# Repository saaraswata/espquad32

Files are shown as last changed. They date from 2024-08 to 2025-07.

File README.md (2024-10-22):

# ESP32-Quadcopter

### Introduction

**ESP32-Quadcopter** is an open source solution based on Espressif ESP32/ESP32-S2/ESP32-S3 Wi-Fi chip, which can be controlled by a mobile APP or gamepad over **Wi-Fi** connection. ESP32-QUADCOPTER comes with **simple hardware**, **clear and extensible code architecture**, and therefore this project can be used in **STEM education** and other fields. The main code is ported from **Crazyflie** open source project with **GPL3.0** protocol.

> Currently support ESP32, ESP32S2, ESP32S3, please using ESP-IDF [release/v4.4](https://docs.espressif.com/projects/esp-idf/en/release-v4.4/esp32/get-started/index.html) branch as your develop environment

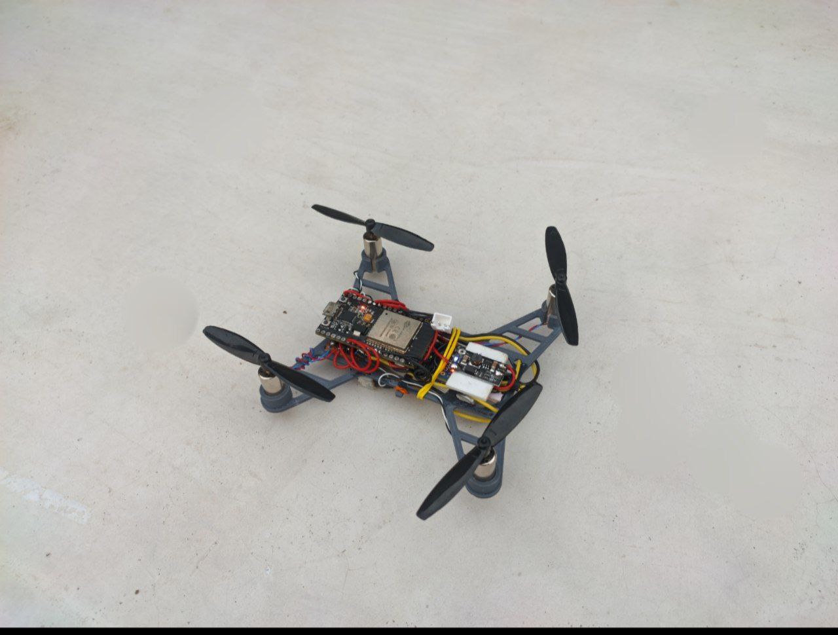
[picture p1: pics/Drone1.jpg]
ESP32-QUADCOPTER


For more information, please check the sections below:
* **Getting Started**: 
* **Hardware Schematic**：
* **iOS APP Source code**: [ESP-Drone-iOS](https://github.com/EspressifApps/ESP-Drone-iOS)
* **Android APP Source code**: [ESP-Drone-Android](https://github.com/EspressifApps/ESP-Drone-Android)

### Features

1. Stabilize Mode
2. Height-hold Mode
3. Altitude-hold Mode
4. Position-hold Mode
5. APP Control
6. CFclient Supported
7. ESP-BOX3 Joystick Control (through esp-now)

Note: to implement Altitude-hold/Height-hold/Position-hold mode, extension boards are needed. For more information, see Hardware Reference. 

### Third Party Copyrighted Code

Additional third party copyrighted code is included under the following licenses.

| Component | License | Origin |Commit ID |
| :---:  | :---: | :---: |:---: |
| core/crazyflie | GPL3.0  |[Crazyflie](https://github.com/bitcraze/crazyflie-firmware) |tag_2021_01 b448553|
| lib/dsp_lib |  | [esp32-lin](https://github.com/whyengineer/esp32-lin/tree/master/components/dsp_lib) |6fa39f4c|

### Support Policy

Any kind of modifications as long as plausible are welcome. Support till 2028.

### THANKS

1. Thanks to Bitcraze for the great [Crazyflie project](https://www.bitcraze.io/%20).
2. Thanks to Espressif for the powerful [ESP-IDF framework](https://docs.espressif.com/projects/esp-idf/en/latest/esp32s2/get-started/index.html).
3. Thanks to WhyEngineer for the useful [ESP-DSP lib](https://github.com/whyengineer/esp32-lin/tree/master/components/dsp_lib).
4. Thanks to Espressif for the ESP-Drone port of Crazyflie firmware.

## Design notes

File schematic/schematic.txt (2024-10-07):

ESP32 GPIO | MPU6050
3v3        |  Vin
Gnd        |  Gnd
32         |  SDA
33         |  SCL
23         |  INT

ESP32 GPIO |   ESC
16         |  Mot_1  
4          |  Mot_2
12         |  Mot_3
14         |  Mot_4

MPU6050 | MS5611
3v3     |  3v3
Gnd     |  Gnd
SDA     |  SDA
SCL     |  SCL

Info about Motors:
Using 8520 brushless Motors. If using 716/715 coreless motors then select 715 from Menuconfig
Mot_1 and Mot_3: CCW
Mot_2 and Mot_4: CW

Info about MPU6050 Placement and Direction:
MPU6050 can be placed anywhere on the drone. The Pinout of the MPU6050 should be on the right side, and this is the position where forward of you is forward of the drone.

NOTE:
* Connecting INT pin is only required for ESP32. ESP32 S2 and S3 don't need this pin to be connected.
* Use High Current rate batteries. I'm using Orange 3.8v 90C/180C 550mah (Best choice) AND/OR Bonka 3.7v 600mah 25C Lipo battery (not so preferred, but flies)
* Pins can be changed from menuconfig

I am getting approx 5 mins of flight time with both the batteries but the drone flies much higher and better with Orange 3.8v 90C/180C lipo cell.
You can also use 1000mah 30C 3.7v batteries.

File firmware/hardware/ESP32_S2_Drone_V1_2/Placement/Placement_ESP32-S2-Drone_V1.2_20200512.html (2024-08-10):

D:\WORK\#31436_ESP32-S2-ESPlane-KIT_M_V1.0_N_XX_20200325_V0.1\#31436_ESP32-S2-ESPlane-KIT_M_V1.2_N_XX_20200511_V0.3\02_PCB/PCB_ESP32-S2-Drone_V1.2_20200512.pcb Create in 2020/5/12 17:13:59 Total components = 203 component(s)

Component Report
NO. | RefDes | PartDecal | Pins | Layer | Orient | PositionX | PositionY | IsSMD
1 | C1 | C0603 | 2 | Top | 180 | 1571.554 | 2462.404 | Yes
2 | C2 | C0402 | 2 | Top | 90 | 1685.304 | 2562.104 | Yes
3 | C3 | C0603 | 2 | Top | 180 | 1555.454 | 2230.404 | Yes
4 | C4 | C0402 | 2 | Top | 270 | 1923.504 | 2559.904 | Yes
5 | C5 | C0402 | 2 | Top | 270 | 1771.004 | 2562.104 | Yes
6 | C6 | C0603 | 2 | Top | 0 | 2787.933 | 2016.722 | Yes
7 | C7 | C0402 | 2 | Top | 0 | 2808.406 | 1922.234 | Yes
8 | C8 | C0603 | 2 | Top | 180 | 2671.004 | 2016.722 | Yes
9 | C9 | C0402 | 2 | Top | 90 | 2750.925 | 1943.888 | Yes
10 | C10 | C0603 | 2 | Top | 180 | 1711.454 | 2230.404 | Yes
11 | C11 | C0603 | 2 | Top | 180 | 1706.504 | 2462.404 | Yes
12 | C12 | C0603 | 2 | Top | 180 | 1426.004 | 2117.254 | Yes
13 | C13 | C0402 | 2 | Top | 0 | 2231.004 | 2304.754 | Yes
14 | C14 | C0603 | 2 | Top | 90 | 2369.754 | 2361.004 | Yes
15 | C15 | C0603 | 2 | Top | 90 | 2169.754 | 2403.504 | Yes
16 | C16 | C0603 | 2 | Top | 180 | 2409.843 | 1237.402 | Yes
17 | C17 | C0402 | 2 | Top | 180 | 2398.031 | 1188.189 | Yes
18 | C18 | C0402 | 2 | Top | 270 | 1571.260 | 1214.173 | Yes
19 | C19 | C0402 | 2 | Top | 270 | 1852.254 | 2286.004 | Yes
20 | C20 | C0402 | 2 | Top | 0 | 2028.839 | 2377.254 | Yes
21 | C21 | C0402 | 2 | Top | 90 | 1959.604 | 2393.504 | Yes
22 | C22 | C0402 | 2 | Top | 180 | 1918.504 | 2141.004 | Yes
23 | C23 | C0402 | 2 | Top | 0 | 1139.370 | 1915.354 | Yes
24 | C24 | C0402 | 2 | Top | 0 | 1139.754 | 1604.754 | Yes
25 | D1 | SOD523 | 2 | Top | 315 | 1382.254 | 1399.754 | Yes
26 | D2 | SOD523 | 2 | Top | 45 | 1389.754 | 2547.254 | Yes
27 | D3 | SOD323 | 2 | Top | 90 | 2376.004 | 2237.254 | Yes
28 | D4 | SOD523 | 2 | Top | 135 | 2549.754 | 2552.254 | Yes
29 | D5 | SOD523 | 2 | Top | 0 | 2744.754 | 1419.754 | Yes
30 | D6 | LED3010-S | 3 | Top | 0 | 1476.378 | 2814.961 | Yes
31 | D7 | LED3010-S | 3 | Top | 180 | 1476.378 | 1122.047 | Yes
32 | D8 | LED3010-S | 3 | Top | 0 | 2460.630 | 2814.961 | Yes
33 | D9 | LED3010-S | 3 | Top | 180 | 2460.630 | 1122.047 | Yes
34 | FB1 | L0603 | 2 | Top | 90 | 2409.754 | 1328.504 | Yes
35 | H1 | P_2X1 | 1 | Bottom | 135 | 2814.964 | 2657.484 | Yes
36 | H58 | P_2X1 | 1 | Bottom | 45 | 708.661 | 3346.457 | Yes
37 | H59 | P_2X1 | 1 | Bottom | 45 | 1279.528 | 2814.961 | Yes
38 | H60 | P_2X1 | 1 | Bottom | 45 | 2657.480 | 1122.047 | Yes
39 | H61 | P_2X1 | 1 | Bottom | 45 | 3228.346 | 590.551 | Yes
40 | H62 | P_2X1 | 1 | Bottom | 135 | 1122.047 | 1279.528 | Yes
41 | H63 | P_2X1 | 1 | Bottom | 45 | 1122.047 | 2657.480 | Yes
42 | H65 | P_2X1 | 1 | Bottom | 45 | 3346.457 | 708.661 | Yes
43 | H66 | P_2X1 | 1 | Bottom | 135 | 2657.480 | 2814.961 | Yes
44 | H67 | P_2X1 | 1 | Bottom | 135 | 1279.528 | 1122.047 | Yes
45 | H68 | P_2X1 | 1 | Bottom | 135 | 590.551 | 708.661 | Yes
46 | H69 | P_2X1 | 1 | Bottom | 45 | 590.551 | 3228.346 | Yes
47 | H70 | P_2X1 | 1 | Bottom | 45 | 2814.961 | 1279.528 | Yes
48 | H71 | P_2X1 | 1 | Bottom | 135 | 3346.457 | 3228.346 | Yes
49 | H72 | P_2X1 | 1 | Bottom | 135 | 708.661 | 590.551 | Yes
50 | H73 | P_2X1 | 1 | Bottom | 135 | 3228.346 | 3346.457 | Yes
51 | J1 | USB_5P_MICRO_F | 11 | Top | 180 | 2638.504 | 2303.504 | No
52 | J2 | FFC24-0P5 | 26 | Top | 180 | 1968.504 | 2736.220 | Yes
53 | J3 | A2005HWV-S-XP-A | 16 | Top | 270 | 2460.630 | 1751.969 | No
54 | J4 | A2005HWV-S-XP-A | 16 | Top | 270 | 1476.378 | 1751.969 | No
55 | J5 | CON2X1_1P5_SMT_ZH-2A_DIP | 4 | Top | 45 | 2678.504 | 2678.504 | No
56 | J6 | CON2X1_1P5_SMT_ZH-2A_DIP | 4 | Top | 315 | 2678.504 | 1258.504 | No
57 | J7 | CON2X1_2P0_SMT_PH2A-S-A | 4 | Top | 270 | 1478.346 | 2288.504 | Yes
58 | J8 | CON2X1_1P5_SMT_ZH-2A_DIP | 4 | Top | 225 | 1258.504 | 1258.504 | No
59 | J9 | CON2X1_1P5_SMT_ZH-2A_DIP | 4 | Top | 135 | 1258.504 | 2678.504 | No
60 | J10 | A2005HWV-S-XP-A | 16 | Top | 270 | 1476.378 | 463.219 | No
61 | J11 | A2005HWV-S-XP-A | 16 | Top | 270 | 2460.630 | 463.219 | No
62 | Q3 | SOT-23-3 | 3 | Top | 180 | 1291.334 | 2033.504 | Yes
63 | Q4 | SOT-23-3 | 3 | Top | 0 | 1218.504 | 1512.004 | Yes
64 | Q5 | SOT-23-3 | 3 | Top | 270 | 1518.504 | 2667.254 | Yes
65 | Q6 | SOT-23-3 | 3 | Top | 90 | 2418.504 | 2667.504 | Yes
66 | Q7 | SOT-23-3 | 3 | Top | 0 | 2718.504 | 1512.004 | Yes
67 | R1 | R0402 | 2 | Top | 180 | 2533.504 | 2143.504 | Yes
68 | R3 | R0402 | 2 | Top | 0 | 2454.754 | 2143.504 | Yes
69 | R5 | R0402 | 2 | Top | 90 | 1868.404 | 2559.904 | Yes
70 | R6 | R0402 | 2 | Top | 270 | 1736.904 | 2562.104 | Yes
71 | R7 | R0402 | 2 | Top | 90 | 2709.193 | 1943.888 | Yes
72 | R8 | R0402 | 2 | Top | 0 | 2808.012 | 1963.967 | Yes
73 | R9 | R0402 | 2 | Top | 0 | 2646.201 | 1929.321 | Yes
74 | R10 | R0402 | 2 | Top | 0 | 2646.201 | 1964.754 | Yes
75 | R11 | R0402 | 2 | Top | 90 | 1321.260 | 1581.890 | Yes
76 | R12 | R0402 | 2 | Top | 90 | 1356.693 | 1581.890 | Yes
77 | R13 | R0402 | 2 | Top | 180 | 1232.254 | 1604.754 | Yes
78 | R14 | R0402 | 2 | Top | 180 | 1675.504 | 2619.904 | Yes
79 | R15 | R0402 | 2 | Top | 90 | 2583.996 | 1996.348 | Yes
80 | R16 | R0402 | 2 | Top | 270 | 2583.996 | 1916.148 | Yes
81 | R17 | R0402 | 2 | Top | 0 | 1253.504 | 2123.504 | Yes
82 | R18 | R0402 | 2 | Top | 180 | 2231.004 | 2267.854 | Yes
83 | R19 | R0402 | 2 | Top | 0 | 1139.754 | 1871.004 | Yes
84 | R20 | R0402 | 2 | Top | 90 | 2287.254 | 2288.504 | Yes
85 | R21 | R0402 | 2 | Top | 180 | 1538.976 | 1357.480 | Yes
86 | R22 | R0402 | 2 | Top | 90 | 1536.614 | 1214.173 | Yes
87 | R23 | R0402 | 2 | Top | 180 | 2381.004 | 2563.504 | Yes
88 | R24 | R0402 | 2 | Top | 90 | 2622.254 | 1529.754 | Yes
89 | R25 | R0402 | 2 | Top | 180 | 1538.976 | 1397.638 | Yes
90 | R26 | R0402 | 2 | Top | 180 | 1516.004 | 2763.504 | Yes
91 | R27 | R0402 | 2 | Top | 0 | 2018.604 | 2121.004 | Yes
92 | R28 | R0402 | 2 | Top | 0 | 1887.254 | 2377.254 | Yes
93 | R29 | R0402 | 2 | Top | 90 | 1448.504 | 1214.754 | Yes
94 | R30 | R0402 | 2 | Top | 180 | 2499.754 | 2763.504 | Yes
95 | R31 | R0402 | 2 | Top | 0 | 2476.772 | 1188.189 | Yes
96 | R32 | R0402 | 2 | Top | 270 | 2086.004 | 2360.504 | Yes
97 | R33 | R0402 | 2 | Top | 90 | 2086.004 | 2280.504 | Yes
98 | R34 | R0402 | 2 | Top | 0 | 1282.254 | 1759.754 | Yes
99 | R35 | R0402 | 2 | Top | 90 | 1344.754 | 1702.254 | Yes
100 | SW1 | SW4_3X3P5X1P1_SMT | 6 | Top | 270 | 1141.704 | 2047.244 | No
101 | SW2 | SW4_3X3P5X1P1_SMT | 6 | Top | 270 | 1141.732 | 1740.157 | No
102 | T1 | K_3X2 | 1 | Top | 0 | 68.504 | 2242.504 | No
103 | T2 | K_3X2 | 1 | Top | 0 | 68.504 | 2095.504 | No
104 | T3 | K_3X2 | 1 | Top | 0 | 720.472 | 2242.504 | No
105 | T4 | K_3X2 | 1 | Top | 0 | 720.472 | 2095.504 | No
106 | T5 | K_3X2 | 1 | Top | 0 | 68.504 | 1841.504 | No
107 | T6 | K_3X2 | 1 | Top | 0 | 68.504 | 1694.504 | No
108 | T7 | K_3X2 | 1 | Top | 0 | 720.474 | 1841.504 | No
109 | T8 | K_3X2 | 1 | Top | 0 | 720.472 | 1694.504 | No
110 | T9 | K_3X2 | 1 | Top | 180 | 1648.504 | 3512.254 | No
111 | T10 | K_3X2 | 1 | Top | 180 | 1648.504 | 3366.004 | No
112 | T11 | K_3X2 | 1 | Top | 180 | 3868.504 | 2242.504 | No
113 | T12 | K_3X2 | 1 | Top | 180 | 3868.504 | 2094.754 | No
114 | T13 | K_3X2 | 1 | Top | 180 | 2276.504 | 3512.254 | No
115 | T14 | K_3X2 | 1 | Top | 180 | 2276.504 | 3366.004 | No
116 | T15 | K_3X2 | 1 | Top | 180 | 3868.504 | 1841.504 | No
117 | T16 | K_3X2 | 1 | Top | 180 | 3868.504 | 1694.754 | No
118 | T17 | K_3X2 | 1 | Top | 0 | 3216.504 | 2242.504 | No
119 | T18 | K_3X2 | 1 | Top | 0 | 3216.504 | 2095.504 | No
120 | T19 | K_3X2 | 1 | Top | 0 | 3216.504 | 1841.504 | No
121 | T20 | K_3X2 | 1 | Top | 0 | 3216.504 | 1694.504 | No
122 | T21 | SMD_3X6 | 1 | Top | 225 | 3359.055 | 495.669 | No
123 | T22 | HOLE_0P6 | 1 | Top | 0 | 717.649 | 2527.559 | No
124 | T23 | SMD_3X6 | 1 | Top | 45 | 3881.102 | 136.220 | No
125 | T24 | SMD_3X6 | 1 | Top | 135 | 3813.386 | 3888.583 | No
126 | T25 | SMD_3X6 | 1 | Top | 315 | 3446.063 | 3375.591 | No
127 | T26 | SMD_3X6 | 1 | Top | 225 | 47.638 | 3812.205 | No
128 | T27 | SMD_3X6 | 1 | Top | 45 | 585.039 | 3433.071 | No
129 | T28 | SMD_3X6 | 1 | Top | 135 | 497.638 | 582.677 | No
130 | T29 | SMD_3X6 | 1 | Top | 315 | 124.409 | 45.669 | No
131 | T30 | HOLE_0P6 | 1 | Top | 0 | 717.649 | 2500.000 | No
132 | T31 | HOLE_0P6 | 1 | Top | 0 | 717.649 | 2472.441 | No
133 | T32 | HOLE_0P6 | 1 | Top | 0 | 717.649 | 2417.323 | No
134 | T33 | HOLE_0P6 | 1 | Top | 0 | 717.649 | 1519.685 | No
135 | T34 | HOLE_0P6 | 1 | Top | 0 | 717.649 | 1492.126 | No
136 | T35 | HOLE_0P6 | 1 | Top | 0 | 717.649 | 1464.567 | No
137 | T36 | HOLE_0P6 | 1 | Top | 0 | 717.649 | 1409.449 | No
138 | T37 | HOLE_0P6 | 1 | Top | 0 | 717.649 | 1437.008 | No
139 | T38 | HOLE_0P6 | 1 | Top | 0 | 1076.772 | 1519.685 | No
140 | T39 | HOLE_0P6 | 1 | Top | 0 | 1076.772 | 1492.126 | No
141 | T40 | HOLE_0P6 | 1 | Top | 0 | 1076.772 | 1464.567 | No
142 | T41 | HOLE_0P6 | 1 | Top | 0 | 1076.772 | 1409.449 | No
143 | T42 | HOLE_0P6 | 1 | Top | 0 | 1076.772 | 1437.008 | No
144 | T43 | HOLE_0P6 | 1 | Top | 0 | 1076.772 | 2531.496 | No
145 | T44 | HOLE_0P6 | 1 | Top | 0 | 1076.772 | 2503.937 | No
146 | T45 | HOLE_0P6 | 1 | Top | 0 | 1076.772 | 2476.378 | No
147 | T46 | HOLE_0P6 | 1 | Top | 0 | 1076.772 | 2448.819 | No
148 | T47 | HOLE_0P6 | 1 | Top | 0 | 1076.772 | 2421.260 | No
149 | T48 | HOLE_0P6 | 1 | Top | 0 | 3219.359 | 2531.496 | No
150 | T49 | HOLE_0P6 | 1 | Top | 0 | 3219.359 | 2503.937 | No
151 | T50 | HOLE_0P6 | 1 | Top | 0 | 3219.359 | 2476.378 | No
152 | T51 | HOLE_0P6 | 1 | Top | 0 | 3219.359 | 2448.819 | No
153 | T52 | HOLE_0P6 | 1 | Top | 0 | 3219.359 | 2421.260 | No
154 | T53 | HOLE_0P6 | 1 | Top | 0 | 3219.359 | 1515.748 | No
155 | T54 | HOLE_0P6 | 1 | Top | 0 | 3219.359 | 1488.189 | No
156 | T55 | HOLE_0P6 | 1 | Top | 0 | 3219.359 | 1460.630 | No
157 | T56 | HOLE_0P6 | 1 | Top | 0 | 3219.359 | 1433.071 | No
158 | T57 | HOLE_0P6 | 1 | Top | 0 | 3219.359 | 1405.512 | No
159 | T58 | HOLE_0P6 | 1 | Top | 0 | 717.649 | 2444.882 | No
160 | T59 | HOLE_0P6 | 1 | Top | 0 | 2860.236 | 1519.685 | No
161 | T60 | HOLE_0P6 | 1 | Top | 0 | 2860.236 | 1492.126 | No
162 | T61 | HOLE_0P6 | 1 | Top | 0 | 2860.236 | 1464.567 | No
163 | T62 | HOLE_0P6 | 1 | Top | 0 | 2860.236 | 1437.008 | No
164 | T63 | HOLE_0P6 | 1 | Top | 0 | 2860.236 | 1409.449 | No
165 | T64 | HOLE_0P6 | 1 | Top | 0 | 2860.236 | 2531.496 | No
166 | T65 | HOLE_0P6 | 1 | Top | 0 | 2860.236 | 2503.937 | No
167 | T66 | HOLE_0P6 | 1 | Top | 0 | 2860.236 | 2476.378 | No
168 | T67 | HOLE_0P6 | 1 | Top | 0 | 2860.236 | 2448.819 | No
169 | T68 | HOLE_0P6 | 1 | Top | 0 | 2860.236 | 2421.260 | No
170 | T69 | HOLE_0P6 | 1 | Top | 0 | 1549.291 | 1074.803 | No
171 | T70 | HOLE_0P6 | 1 | Top | 0 | 1576.850 | 1074.803 | No
172 | T71 | HOLE_0P6 | 1 | Top | 0 | 1604.409 | 1074.803 | No
173 | T72 | HOLE_0P6 | 1 | Top | 0 | 1631.969 | 1074.803 | No
174 | T73 | HOLE_0P6 | 1 | Top | 0 | 1549.291 | 925.197 | No
175 | T74 | HOLE_0P6 | 1 | Top | 0 | 1576.850 | 925.197 | No
176 | T75 | HOLE_0P6 | 1 | Top | 0 | 1604.409 | 925.197 | No
177 | T76 | HOLE_0P6 | 1 | Top | 0 | 1631.969 | 925.197 | No
178 | T77 | HOLE_0P6 | 1 | Top | 0 | 2305.315 | 925.197 | No
179 | T78 | HOLE_0P6 | 1 | Top | 0 | 2332.874 | 925.197 | No
180 | T79 | HOLE_0P6 | 1 | Top | 0 | 2360.433 | 925.197 | No
181 | T80 | HOLE_0P6 | 1 | Top | 0 | 2387.992 | 925.197 | No
182 | T81 | HOLE_0P6 | 1 | Top | 0 | 2305.315 | 1074.803 | No
183 | T82 | HOLE_0P6 | 1 | Top | 0 | 2332.874 | 1074.803 | No
184 | T83 | HOLE_0P6 | 1 | Top | 0 | 2360.433 | 1074.803 | No
185 | T84 | HOLE_0P6 | 1 | Top | 0 | 2387.992 | 1074.803 | No
186 | T85 | HOLE_0P6 | 1 | Top | 0 | 1913.386 | 3464.567 | No
187 | T86 | HOLE_0P6 | 1 | Top | 0 | 1940.945 | 3464.567 | No
188 | T87 | HOLE_0P6 | 1 | Top | 0 | 1968.504 | 3464.567 | No
189 | T88 | HOLE_0P6 | 1 | Top | 0 | 1996.063 | 3464.567 | No
190 | T89 | HOLE_0P6 | 1 | Top | 0 | 2023.622 | 3464.567 | No
191 | T91 | HOLE_0P6 | 1 | Top | 0 | 1913.386 | 2862.205 | No
192 | T92 | HOLE_0P6 | 1 | Top | 0 | 1940.945 | 2862.205 | No
193 | T93 | HOLE_0P6 | 1 | Top | 0 | 1968.504 | 2862.205 | No
194 | T94 | HOLE_0P6 | 1 | Top | 0 | 1996.063 | 2862.205 | No
195 | T95 | HOLE_0P6 | 1 | Top | 0 | 2023.622 | 2862.205 | No
196 | U1 | SOT23-6 | 6 | Top | 270 | 2493.504 | 2253.504 | Yes
197 | U2 | SOT-23-5 | 5 | Top | 90 | 1500.354 | 2313.104 | Yes
198 | U3 | QFN28_0P5_5 | 29 | Top | 180 | 2688.720 | 1776.959 | Yes
199 | U4 | SOT-23-5 | 5 | Top | 90 | 1656.354 | 2313.104 | Yes
200 | U5 | DFN3030-8 | 9 | Top | 270 | 2264.754 | 2392.254 | Yes
201 | U6 | ESP32-S2-WROVER | 43 | Top | 180 | 2322.835 | 834.646 | Yes
202 | U7 | QFN24_0P5_4_A | 24 | Top | 180 | 1968.504 | 2256.204 | Yes
203 | U8 | SOT363 | 6 | Top | 90 | 1284.754 | 1689.754 | Yes

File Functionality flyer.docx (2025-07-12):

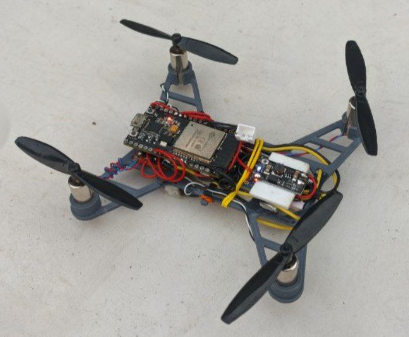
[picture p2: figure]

#### ESP32-Quadcopter Drone

ESP32-Quadcopter is a palm-sized drone project built using ESP32 Wi-Fi microcontrollers, custom-made flight controller and ESC (Electronic Speed Controller) PCBs, and is developed using ESP-IDF. The drone is designed for control via a mobile app over Wi-Fi, and is cost-efficiency, with simple hardware and clear, extensible code architecture.

Why Drones?

Drones are at the forefront of future technology. From agriculture to logistics, defence to filmmaking, autonomous and semi-autonomous drones are reshaping how tasks are approached across numerous industries. As the number of fields adopting drone technology continues to grow, early exposure to these systems becomes essential for staying prepared and contributing meaningfully to the next wave of innovation.

##### Features and Hardware:

Modes | Description | Modules
Stabilize Mode | Maintains stable flight using accelerometer and gyroscopic sensor data. | MPU6050 IMU (Inertial Measurement Unit)
Height-hold Mode | Maintains a fixed flight height using Time-of-flight (ToF) distance sensor data. | VL53L0X/VL53L1X ToF ranging sensor
Altitude-hold Mode | Maintains constant altitude relative to sea level using barometric data. | BMP280 or MS5611 Barometric pressure sensor
Position-hold Mode | Holds drone at a set position using optical flow sensor and Time-of-flight (ToF) distance sensor data. | PMW3901MB-TXQT optical motion tracking sensor, VL53L0X/VL53L1X ToF ranging sensor
Hover Mode | Holds drone at set position and height using optical flow sensor and Time-of-flight (ToF) distance sensor data. | PMW3901MB-TXQT optical motion tracking sensor, VL53L0X/VL53L1X ToF ranging sensor
App Control | Operate and fine-tune the drone via a mobile app. Connect to the drone using a phone via Wi-Fi. | Wi-Fi enabled ESP32 microcontroller
CFclient Supported | Uses Crazyflie’s flight control and tuning software. | Crazyflie client software

##### Potential use-cases:

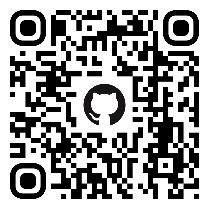
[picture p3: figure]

1. STEM Education: Learn about embedded systems, flight control, sensor integration, and wireless communication in a cost-efficient way while making this project.

YouTube GitHub

2. Recreational Flying and Drone Racing: Enjoy remote-controlled flight using a phone or joystick.

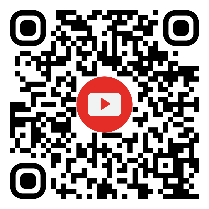
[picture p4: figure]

3. Disaster Rescue: Its small form-factor allows entry into collapsed buildings for gathering information.

4. Emergency Deliveries: Can be quickly deployed to deliver medicines and vaccines over short distances in times of emergency.

5. Agricultural Surveying: Can be adapted for crop health analysis or livestock monitoring over small farmland areas using thermal or NDVI cameras.

6. Environmental Monitoring: Attach temperature, gas, or air quality sensors to monitor environmental conditions in hard-to reach areas like forests, rooftops, or industrial sites.

7. Aerial Photography/Videography and Surveillance: With a lightweight camera module, this drone can capture images or videos from unique angles for documentation, mapping, or remote surveillance.

8. Plug-and-play kits: Can be made into an intuitive plug-and-play assembly kit for children to help them make their own drones by simply connecting the various modules and parts.

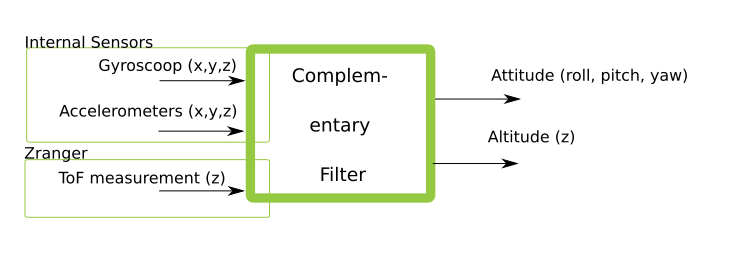
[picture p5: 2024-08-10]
firmware/docs/_static/Schematic-overview-of-inputs-and-outputs-of-the-Complementary-filter.png

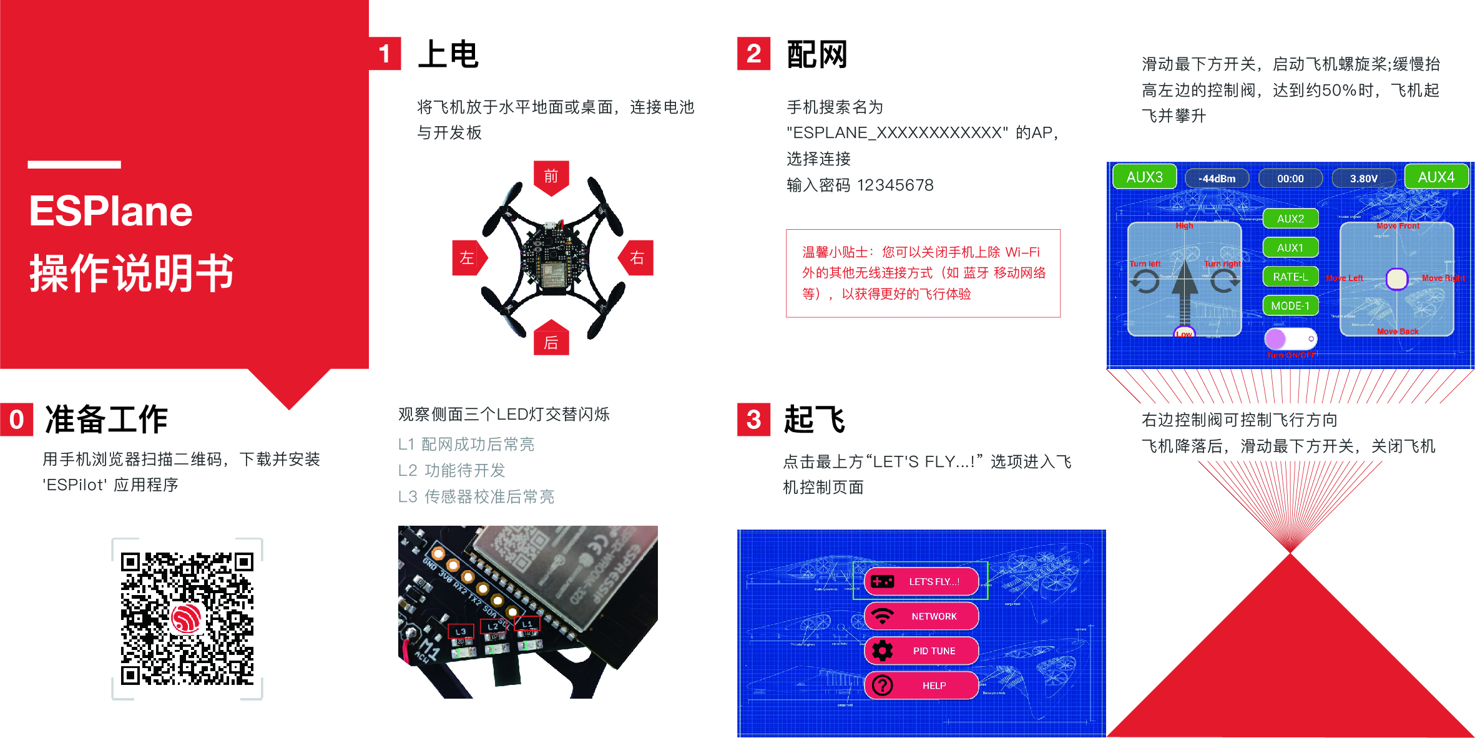
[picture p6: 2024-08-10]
firmware/docs/_static/esplane_v1_specification.jpg

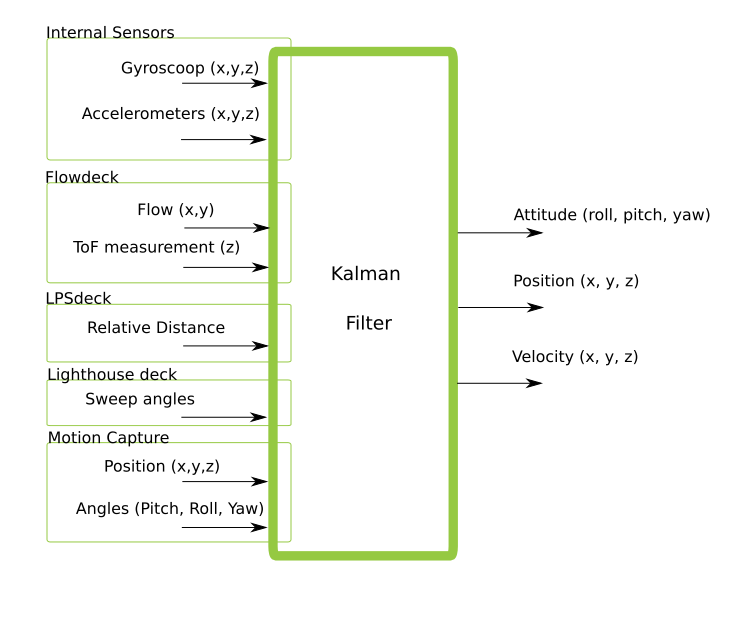
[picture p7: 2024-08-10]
firmware/docs/_static/Schematic-overview-of-inputs-and-outputs-of-the-Extended-Kalman-Filter.png

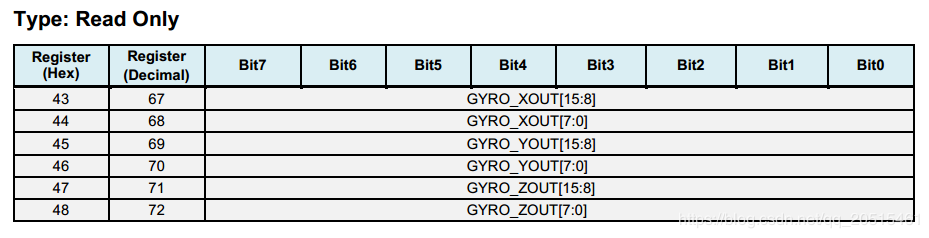
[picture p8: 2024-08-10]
firmware/docs/_static/REG_43_48.png

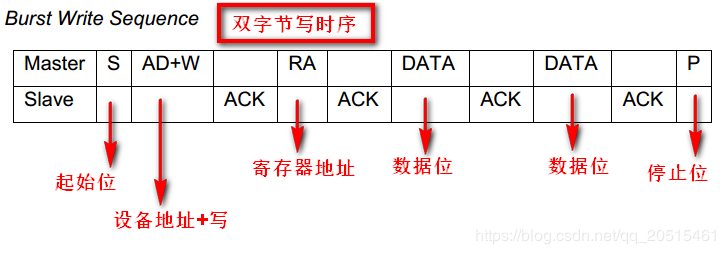
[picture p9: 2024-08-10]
firmware/docs/_static/burst_write_sequence.png

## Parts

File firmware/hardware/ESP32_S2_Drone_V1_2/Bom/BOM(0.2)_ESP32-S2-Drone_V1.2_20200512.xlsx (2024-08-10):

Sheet: ESP32-S2-Drone
BOM(V0.2)_ESP32-S2-Drone_V1.2
ID | Qty | Ref Des | Value | Package | Description | Manufacturer | Manufacturer Part # | Notes
1 | 8 | C1,C3,C10,C11,C12,C14,C15,C16 | 10uF/10V | C0603 | 陶瓷电容
2 | 9 | C2,C4,C5,C7,C9,C17,C18,C19,C21 | 0.1uF/10V | C0402 | 陶瓷电容
3 | 2 | C6,C8 | 4.7uF/10V | C0603 | 陶瓷电容
4 | 1 | C13 | 470pF/25V | C0402 | 陶瓷电容
5 | 1 | C20 | 10nF/25V | C0402 | 陶瓷电容
6 | 1 | C22 | 2.2nF/25V | C0402 | 陶瓷电容
7 | 0 | C23,C24 | 0.1uF/10V(NC) | C0402 | 陶瓷电容 |  |  | 不贴件
8 | 4 | D1,D2,D4,D5 | 1N4148WT | SOD523 | 开关二极管 | 长电科技 | 1N4148WT
9 | 1 | D3 | BAT60B | SOD323 | 肖特基二极管 | Infineon | BAT60B
10 | 1 | D6 | LED-WHT | LED3010-S | LED,白色 | Everlight | 12-21/T3D-APQHY/2C
11 | 1 | D7 | LED-BLE | LED3010-S | LED,蓝色 | Everlight | 12-21/BHC-ZL2N1TY/2C
12 | 1 | D8 | LED-RED | LED3010-S | LED,红色 | Everlight | 12-21/R8C-AN1P2B/2D
13 | 1 | D9 | LED-GRN | LED3010-S | LED,绿色 | Everlight | 12-21/GHC-YQ1R1B18Y/2C
14 | 1 | FB1 | BLM18SG331TN1D | L0603 | 磁珠,330R at 100MHz,1A | Murata | BLM18SG331TN1D
15 | 1 | J1 | USB-MICRO-B | USB_5P_MICRO_F | USB MicroB 连接器,四脚插板,无柱,卷边
16 | 1 | J2 | FFC-24P | FFC24-0P5 | FPC连接器,24P,间距0.5MM,翻盖式,下接
17 | 4 | J3,J4,J10,J11 | CON8-S-2P54 | A2005HWV-S-XP-A | 单排排母,8P,间距2.0mm,错位贴片,A型 | 长江连接器 | A2005HWV-S-8P-A
18 | 0 | J5,J6,J8,J9 | CON2-SB-ZH(NC) | CON2X1_1P5_SMT_ZH-2A_DIP | 针座,2P,ZH,侧入贴片 |  |  | 不贴件
19 | 1 | J7 | CON2-SB-PH | CON2X1_2P0_SMT_PH2A-S-A | 针座,2P,PH,侧入贴片
20 | 1 | Q3 | AO3401A | SOT-23-3 | PMOS | AOS | AO3401A
21 | 4 | Q4,Q5,Q6,Q7 | IRLML6344TRPbF | SOT-23-3 | Power NMOS | Infineon | IRLML6344TRPbF
22 | 3 | R1,R3,R6 | 0R/1% | R0402 | 贴片电阻
23 | 19 | R5,R8,R11,R12,R13,R14,R15,R16,R21,R22,R23,R24,R25,R27,R28,R32,R33,R34,R35 | 10K/1% | R0402 | 贴片电阻
24 | 1 | R7 | 22.1K/1% | R0402 | 贴片电阻
25 | 1 | R9 | 47.5K/1% | R0402 | 贴片电阻
26 | 3 | R10,R17,R19 | 82K/1% | R0402 | 贴片电阻
27 | 1 | R18 | 52.3K/1% | R0402 | 贴片电阻
28 | 1 | R20 | 29.4K/1% | R0402 | 贴片电阻
29 | 4 | R26,R29,R30,R31 | 1.5K/1% | R0402 | 贴片电阻
30 | 2 | SW1,SW2 | Button-3X3.5 | SW4_3X3P5X1P1_SMT | 轻触开关,侧按贴片,3mmX3.5mm | ALPS | SKSCLBE010
31 | 1 | U1 | USBLC6-2SC6 | SOT23-6 | ESD二极管 | ST | USBLC6-2SC6
32 | 1 | U2 | ME6211C28M5G-N | SOT-23-5 | LDO,2.8V | 微盟 | ME6211C28M5G-N
33 | 1 | U3 | CP2102N-A02 | QFN28_0P5_5 | USB to UART IC | Silicon Labs | CP2102N-A02
34 | 1 | U4 | ME6211C15M5G-N | SOT-23-5 | LDO,1.5V | 微盟 | ME6211C15M5G-N
35 | 1 | U5 | SGM2205-ADJ | DFN3030-8 | LDO,可调 | 圣邦微 | SGM2205-ADJ
36 | 1 | U6 | ESP32-S2-WROVER | ESP32-S2-WROVER | WiFi Module | Espressif | ESP32-S2-WROVER
37 | 1 | U7 | MPU-6050 | QFN24_0p5_4_A | 6轴运动传感器IC | InvenSense | MPU-6050
38 | 1 | U8 | BC847BDW1T1G | SOT363 | NPN Transistor,双路 | ON Semi | BC847BDW1T1G
39 | 1 | 非贴片物料 | 无人机锂电池 | NA | 动力型,300mAh,PH2.0,正向 |  |  | 参考链接 https://m.tb.cn/h.V8gEksR?sm=858897
40 | 4 | 非贴片物料 | 空心杯电机 | NA | 尺寸716,电压3.7v,50000转 |  |  | 参考链接 https://m.tb.cn/h.VR4sgSA?sm=2d0222
41 | 2 | 非贴片物料 | 螺旋桨A | NA | 尺寸46mm,0.75mm孔径,A螺旋桨 |  |  | 参考链接 https://m.tb.cn/h.VinQLQu?sm=185f2b
42 | 2 | 非贴片物料 | 螺旋桨B | NA | 尺寸46mm,0.75mm孔径,B螺旋桨 |  |  | 参考链接 https://m.tb.cn/h.VinQLQu?sm=185f2b
43 | 4 | 非贴片物料 | 电机密封圈 | NA | 孔径7mm,黑色 |  |  | 参考链接 https://m.tb.cn/h.VRfYUIN?sm=1dbc9d

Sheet: Sheet2
39 | 1 | NA | 无人机锂电池 | NA | 动力型300mah PH2.0 正向 | 参考链接 https://m.tb.cn/h.V8gEksR?sm=858897
40 | 4 | NA | 空心杯电机 | NA | 尺寸716 电压3.7v 50000 | 参考链接 https://m.tb.cn/h.VR4sgSA?sm=2d0222
41 | 2 | NA | 螺旋桨A | NA | 尺寸46mm 0.75mm孔径 A螺旋桨 | 参考链接 https://m.tb.cn/h.VinQLQu?sm=185f2b
42 | 2 | NA | 螺旋桨B | NA | 尺寸46mm 0.75mm孔径 B螺旋桨 | 参考链接 https://m.tb.cn/h.VinQLQu?sm=185f2b
43 | 4 | NA | 电机密封圈 | NA | 7mm孔径黑色 | 参考链接 https://m.tb.cn/h.VRfYUIN?sm=1dbc9d

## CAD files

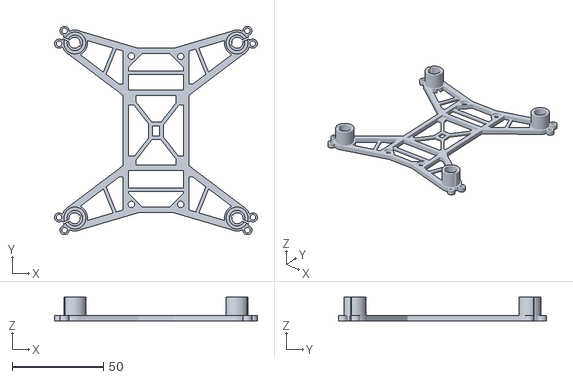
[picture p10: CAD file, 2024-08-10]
frame/FE2G7MWIGL8J36N.stl
111.1 x 114.1 x 13.0

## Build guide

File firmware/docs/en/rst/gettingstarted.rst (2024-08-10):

================
Get Started 
================

:link_to_translation:`zh_CN:[中文]`

ESP-Drone Overview
======================

ESP-Drone is an ESP32/ESP32-S2/ESP32-S3 based flying development board provided by Espressif. ESP-Drone is equipped with Wi-Fi key features, which allows this drone to be connected to and controlled by an APP or a gamepad over a Wi-Fi network. This drone comes with simple-structured hardware, clear codes, and supports functional extension. Therefore, ESP-Drone can be used in STEAM education. Part of the codes is from Crazyflie open source project under GPL3.0
license.

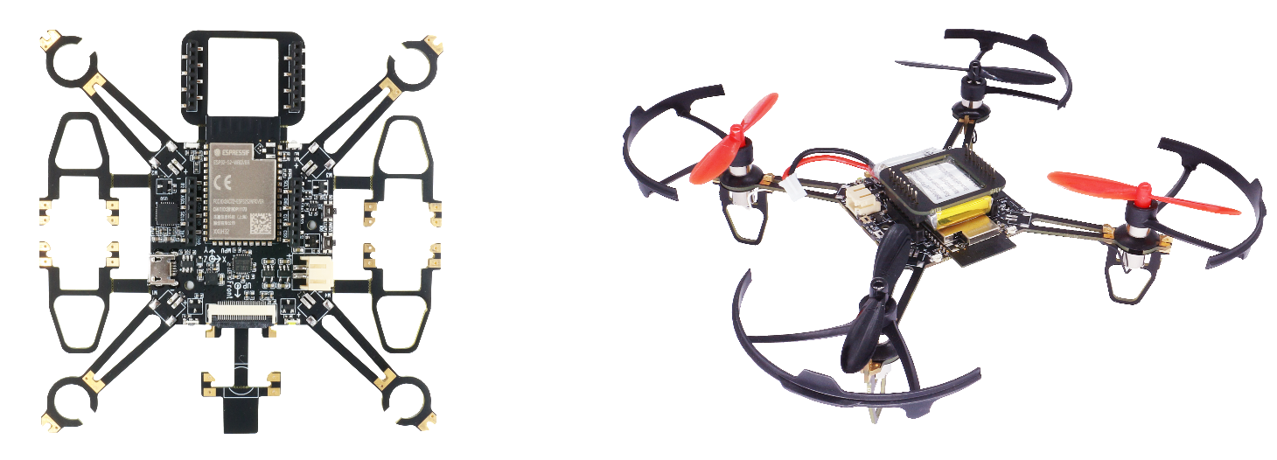
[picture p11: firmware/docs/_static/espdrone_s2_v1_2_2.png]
ESP-Drone

   
   ESP-Drone

Main Features
----------------

ESP-Drone has the following features:

- Stabilize mode: keep the drone stable to achieve smooth flight.
- Height-hold mode: control thrust output to keep the drone flying at a fixed height.
- Position-hold mode: keep the drone flying at a fixed position.
- PC debugging: use cfclient for static/dynamic debugging.
- Controlled by APP: easily controlled over Wi-Fi by your mobile APP.
- Controlled by gamepad: easily controlled via the gamepad by cfclient.

Main Components
----------------

ESP-Drone 2.0 consists of a main board and several extension boards:

-  **Main board**: integrates an ESP32-S2 module, necessary sensors for basic flight, and provides hardware extension interfaces.
-  **Extension boards**: integrate extension sensors via hardware extension interfaces of the main board, to implement advanced flight.  

.. list-table:: 
   :widths: 4 20 15 15 10 10
   :header-rows: 1

   * - No.
     - Modules
     - Main Components
     - Function
     - Interfaces
     - Mount Location
   * - 1
     - Main board - **ESP32-S2**
     - ESP32-S2-WROVER + MPU6050
     - Basic flight
     - I2C, SPI, GPIO, extension interfaces
     - 
   * - 2
     - Extension board - **Position-hold module**
     - PMW3901 + VL53L1X
     - Indoor position-hold flight
     - SPI + I2C
     - Mount at bottom, facing to the ground.
   * - 3
     - Extension board - **Pressure module**
     - MS5611 pressure module
     - Height-hold flight
     - I2C or MPU6050 slave
     - Mount at the top or at the bottom
   * - 4
     - Extension board - **Compass module**
     - HMC5883 compass
     - Advanced flight mode, such as head-free mode
     - I2C or MPU6050 slave
     - Mount at the top or at the bottom

For more information, please refer to `Hardware Reference <./hardware.rst>`__.

ESP-IDF Overview
================

ESP-IDF is the IoT Development Framework provided by Espressif for ESP32/ESP32-S2/ESP32-S3.

- ESP-IDF is a collection of libraries and header files that provides the core software components that are required to build any software projects on ESP32/ESP32-S2.

- ESP-IDF also provides tools and utilities that are required for typical developer and production use cases, like build, flash, debug and measure. 

For more information, please check `ESP-IDF
Programming Guide <https://docs.espressif.com/projects/esp-idf/en/release-v4.4/esp32s2/get-started/index.html>`__.

Crazyflie Overview
=======================

Crazyflie is a Bitcraze open-source quadcopter, with the following features:

- Support various sensor combinations for advanced flight modes, such as Height-hold mode and Position-hold mode.
- Based on FreeRTOS, which allows users to break down complex drone systems into multiple software tasks with various priorities.
- Customized full-featured cfclient and CRTP communication protocol, for debug, measurement, and control purposes.

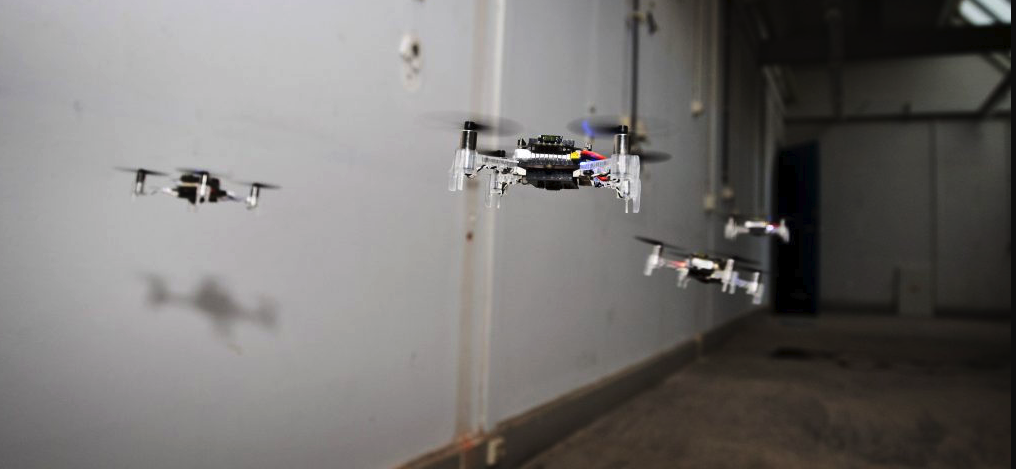
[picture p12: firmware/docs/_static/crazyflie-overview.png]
crazyflie-overview

   
   `A swarm of drones exploring the environment, avoiding obstacles
   and each other. (Guus Schoonewille, TU Delft) <https://img-blog.csdnimg.cn/20191030202634944.jpg?x-oss-process=image/watermark,type_ZmFuZ3poZW5naGVpdGk,shadow_10,text_aHR0cHM6Ly9ibG9nLmNzZG4ubmV0L3FxXzIwNTE1NDYx,size_16,color_FFFFFF,t_70>`__

For more information, see `Crazyflie <https://www.bitcraze.io/>`__.

Preparations
================

Assemble Hardware
--------------------

Please follow the steps below to assemble ESP32-S2-Drone V1.2.

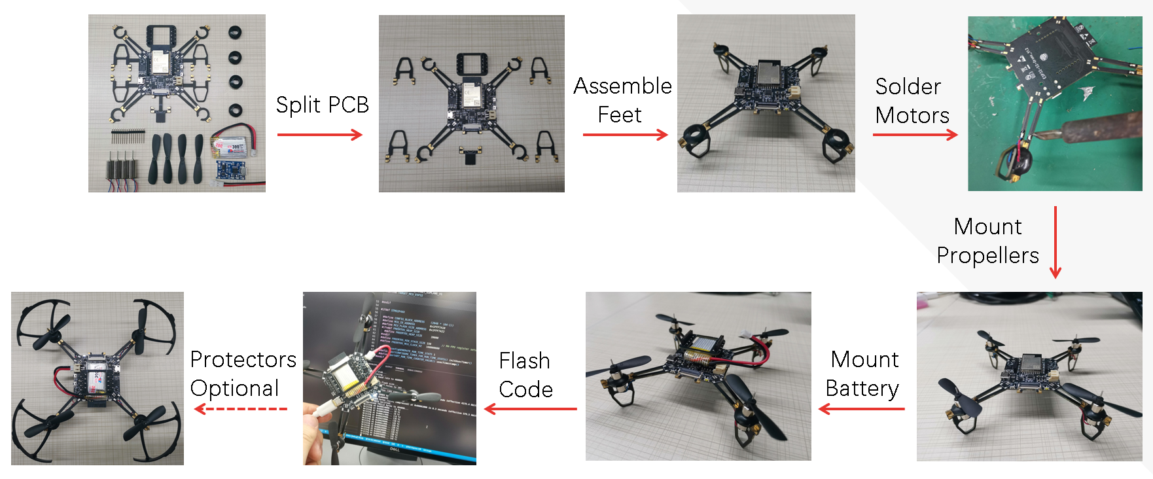
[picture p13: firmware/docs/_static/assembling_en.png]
ESP32-S2-Drone V1.2 Assemble Flow

   
   ESP32-S2-Drone V1.2 Assemble Flow

Hardware overview and pin allocation are available at: `Hardware Reference <./hardware.rst>`__.

Download and Install ESP-Drone APP
----------------------------------------
ESP-Drone APP is available for Android and iOS.

For Android, please scan the QR below to download ESP-Drone APP.

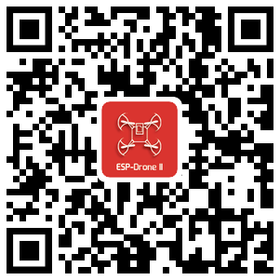
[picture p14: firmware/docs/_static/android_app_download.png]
Android APP QR


For iOS, please search and download the ESP-Drone APP in App Store.

iOS APP source code:
`ESP-Drone-iOS <https://github.com/EspressifApps/ESP-Drone-iOS>`__

Android APP source code:
`ESP-Drone-Android <https://github.com/EspressifApps/ESP-Drone-Android>`__

Install cfclient
--------------------

This step is optional, only for advanced debugging.

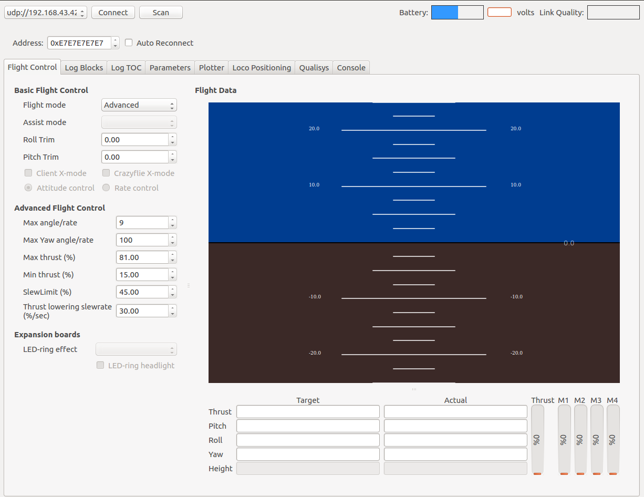
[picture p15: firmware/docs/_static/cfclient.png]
cfclient Interface


   cfclient Interface

**1. Install CRTP protocol package**

1.1 Download the source code

.. code:: text

   git clone -b esp-drone  https://github.com/qljz1993/crazyflie-lib-python.git

1.2 Navigate to the source code directory, and install the requirements

.. code:: text

   pip3 install -r requirements.txt

1.3 Install CRTP package

.. code:: text

   pip3 install -e .

**2. Install cfclient**

2.1 Download the source code

.. code:: text

   git clone -b esp-drone https://github.com/qljz1993/crazyflie-clients-python.git

2.2 Navigate to the source code directory, and install the requirements

.. code:: text

   sudo apt-get install python3 python3-pip python3-pyqt5 python3-pyqt5.qtsvg

2.3 Install cfclient

.. code:: text

   pip3 install -e .

2.4 Start cfclient

.. code:: text

   python3 ./bin/cfclient

**3. Configure the controllers**

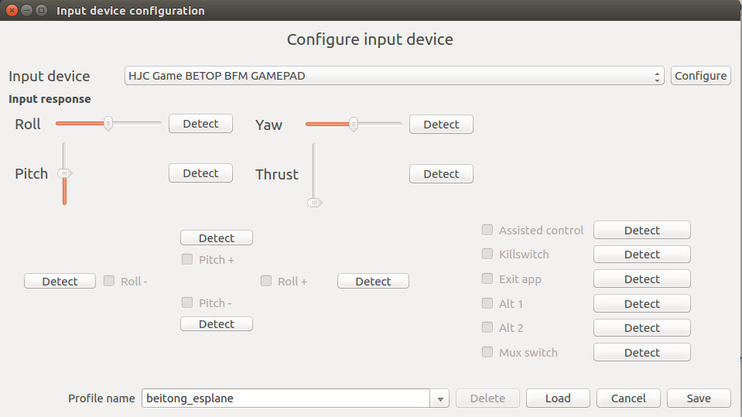
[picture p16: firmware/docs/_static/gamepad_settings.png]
Controller Configuration


   Controller Configuration

3.1 Configure the four main dimensions of controls: ``Roll, Pitch, Yaw, Thrust``.

3.2 Configure button ``Assisted control`` for flight mode switching.

ESP-Drone APP Guide
=====================

Establish Wi-Fi connection
---------------------------
* Scan Wi-Fi AP on your mobile. ESP-Drone device works as a Wi-Fi AP with the following SSID:  

::

   SSID: ESP-DRONE_XXXX (XXXX is configured based on MAC) PASSWORD: 12345678

* Click this AP, connect your mobile to this AP.

Now a Wi-Fi connection is established between your mobile and your drone.

Customize settings
---------------------------
In this step, you can customize the flight settings according to your application scenarios, or use the default configuration below.

::

   ```
   Default configuration:

   Flight control settings 
       1. Mode: Mode2
       2. Deadzone: 0.2
       3. Roll trim: 0.0
       4. Pitch trim: 0.0
       5. Advanced flight control: true
       6. Advanced flight control preferences 
           1. max roll/pitch angle: 15
           2. max yaw angle: 90
           3. max thrust: 90
           4. min thrust: 25
           5. X-Mode: true
   Controller settings 
       1. use full travel for thrust: false
       2. virtual joystick size: 100
   App settings
       1. Screen rotation lock: true
       2. full screen mode:true
       3. show console: true   
   ```

Flight Control
---------------------

- Click “Connect” button/icon at your APP. When the connection is established successfully between your drone and APP, the LED on the drone blinks GREEN.
- Slide “Thrust” slightly to take off the drone.
- Control the flight by moving your fingers on the APP.

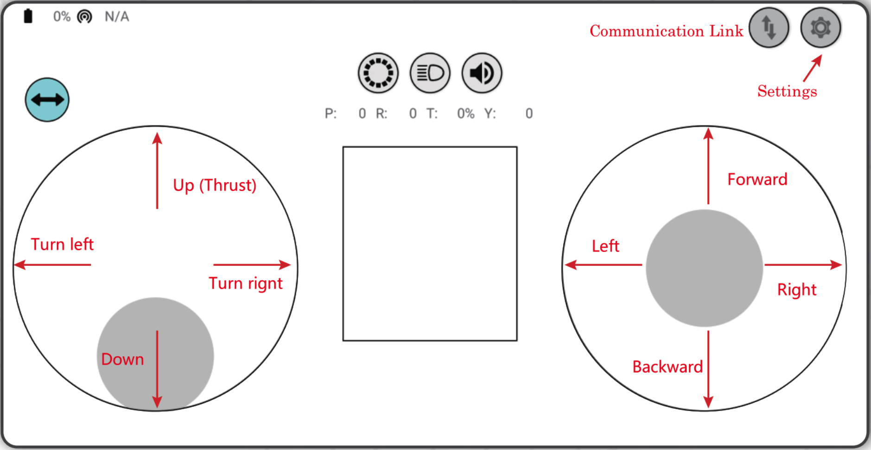
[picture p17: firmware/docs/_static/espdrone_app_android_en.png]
Android APP Interface


   Android APP Interface

PC cfclient Guide
======================

Cfclient is the PC client for ``Crazeflie`` source project, which has fully implemented the functions defined in ``CRTP`` and makes the drone debugging faster. ESP-Drone customizes this cfclient to meet functional design needs.

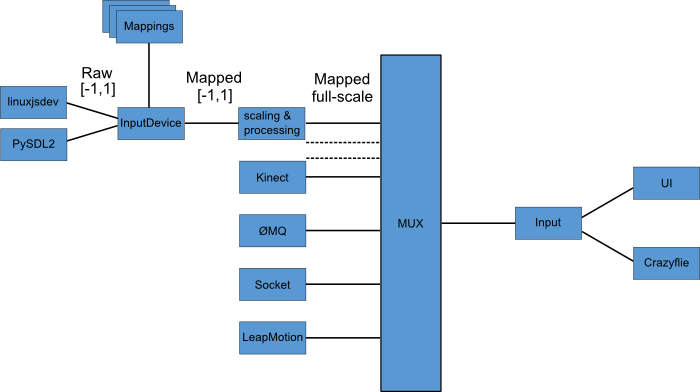
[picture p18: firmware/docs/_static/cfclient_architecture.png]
cfclient architecture


   Cfclient Architecture

cfclient console interface

   Cfclient Console Interface

In this project, we have configuration files and cache files. JSON file is used to store configuration information. For more information about the configuration, please refer to `User
Configuration File <https://www.bitcraze.io/documentation/repository/crazyflie-clients-python/master/development/dev_info_client/>`__.

Flight Settings
--------------------

Basic Flight Control
~~~~~~~~~~~~~~~~~~~~~~

1. Flight mode: normal and advanced modes

   - Normal mode: for beginners.
   - Advanced mode: unlock the maximum angle and the maximum thrust.

2. Assisted mode

   - Altitude-hold mode: maintain flight altitude. To implement this mode, a barometric pressure sensor is needed.
   - Position-hold mode: maintain current flight position. To implement this mode, an optical flow sensor and a Time of Flight (TOF) sensor are needed.
   - Height-hold mode: keep flight height. Note: to apply this mode, the drone should fly at 40 cm or higher over the ground, and a TOF is needed.
   - Hover mode: stay and hover at 40 cm or higher over the take-off point. To implement this mode, a optical flow sensor and a TOF are needed.

3. Trim

   - Roll Trim: trim the rotation around a horizontal axis going through the drone from back to front. This rotation literally rolls the drone and moves it left and right. Roll trim is used to compensate for the level installation deviation of sensors.
   - Pitch Trim: trim the rotation around a horizontal axis going through the drone from left to right. This rotation tilts the drone and moves it forwards or backwards. Pitch trim is used to compensate for the level installation deviation of sensors.

Note that in assisted mode, the thrust controller works as a height controller.

Advanced Flight Control
~~~~~~~~~~~~~~~~~~~~~~~~

1. Max angle: set the maximum pitch and roll rotation: roll/pitch.
2. Max yaw rate: set the allowed yaw: ``yaw``.
3. Max thrust: set the maximum thrust.
4. Min thrust: set the minimum thrust.
5. Slew limit: prevent sudden drop of thrust. When the thrust drops below this limit, the rates below ``Slew rate`` will not be allowed.
6. Slew rate: this is the maximum rate when the thrust is below ``slew limit``.

Configure Input Device
~~~~~~~~~~~~~~~~~~~~~~~~~~~~~

Follow the prompts, route the controllers to each channel.

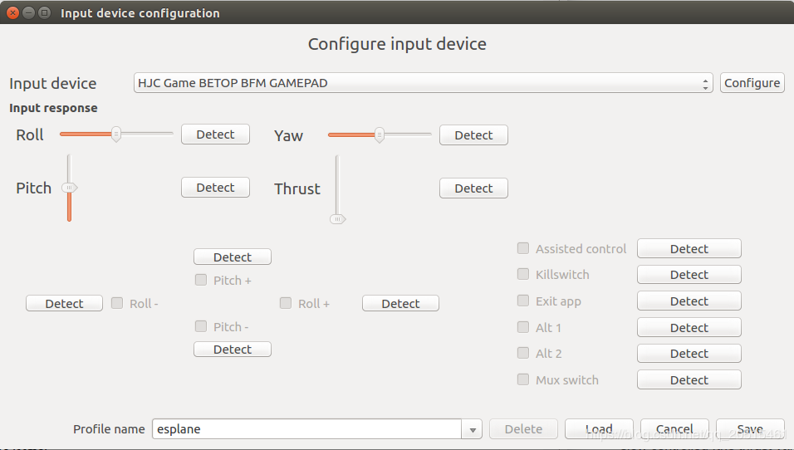
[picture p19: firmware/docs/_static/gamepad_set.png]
cfclient input device configuration


   Cfclient Input Device Configuration

Flight Data
~~~~~~~~~~~~~~~~

On the tab “Flight Control” of cfclient, you can check the drone status. The detailed information is shown at the bottom right, including:

1. Target: target angle
2. Actual: measured angle
3. Thrust: current thrust value
4. M1/M2/M3/M4: actual output of motors

Tune Online Parameters
--------------------------

**Tune PID parameters online**

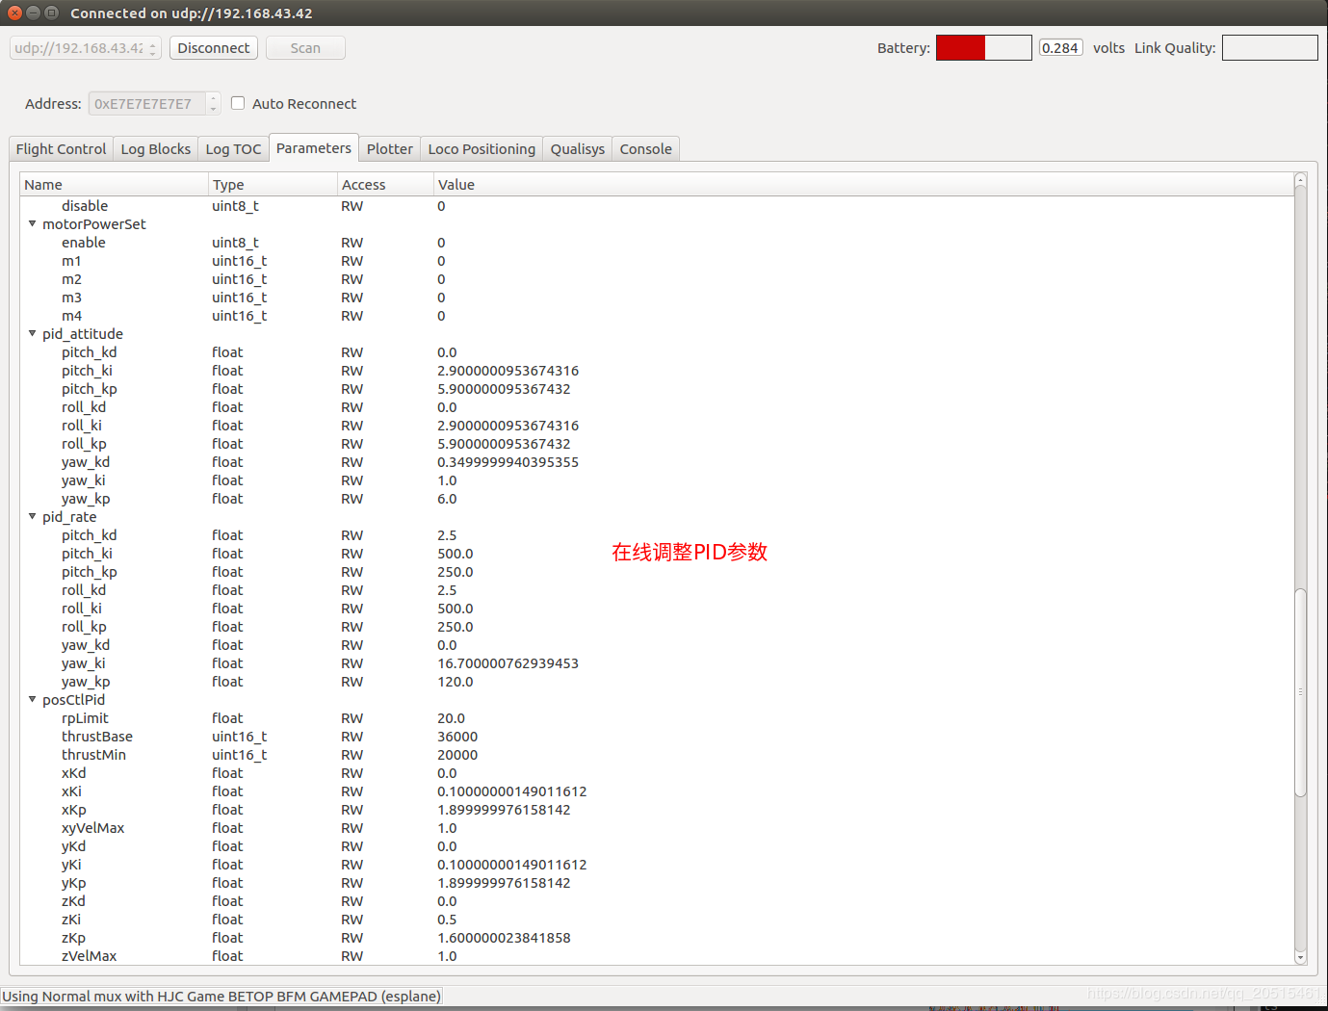
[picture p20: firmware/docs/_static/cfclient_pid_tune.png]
PID parameters tunning

   
   Cfclient PID Parameters Tunning

**Note**

1. The modified parameters take effect in real time, which avoids frequent flash of firmware.
2. You can define in your code which parameters can be modified by PC in real time.
3. Note that modifying parameters online is only for debugging purpose. The modified parameters will not be saved at power down.

Monitor Flight Data
-----------------------

Configure the parameters to monitor at Tab Log configuration and Tab Log Blocks:

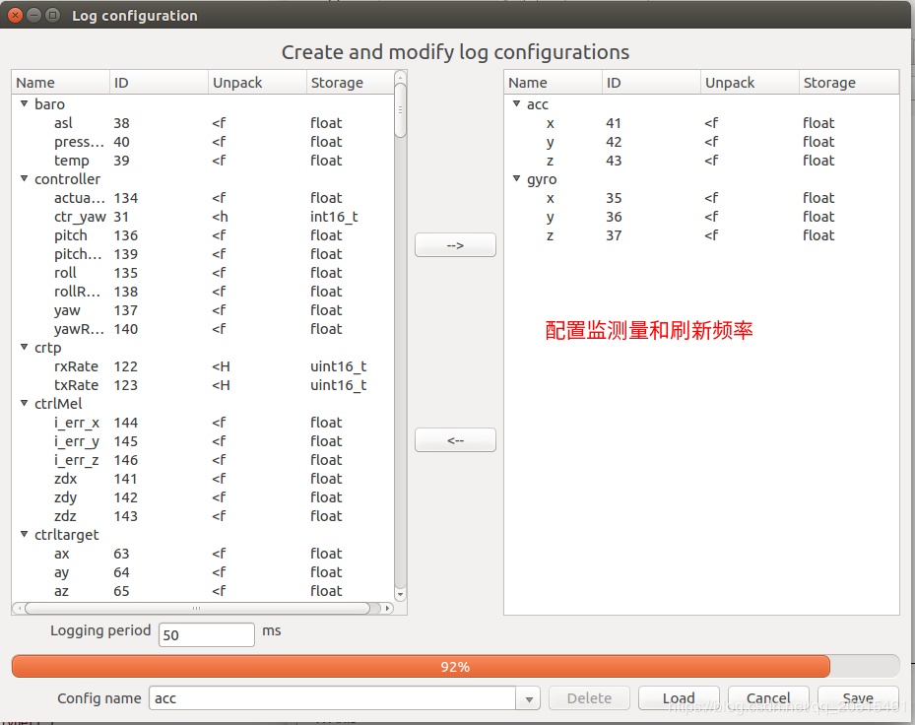
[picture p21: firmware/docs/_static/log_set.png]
Log configuration

   
   Log Configuration

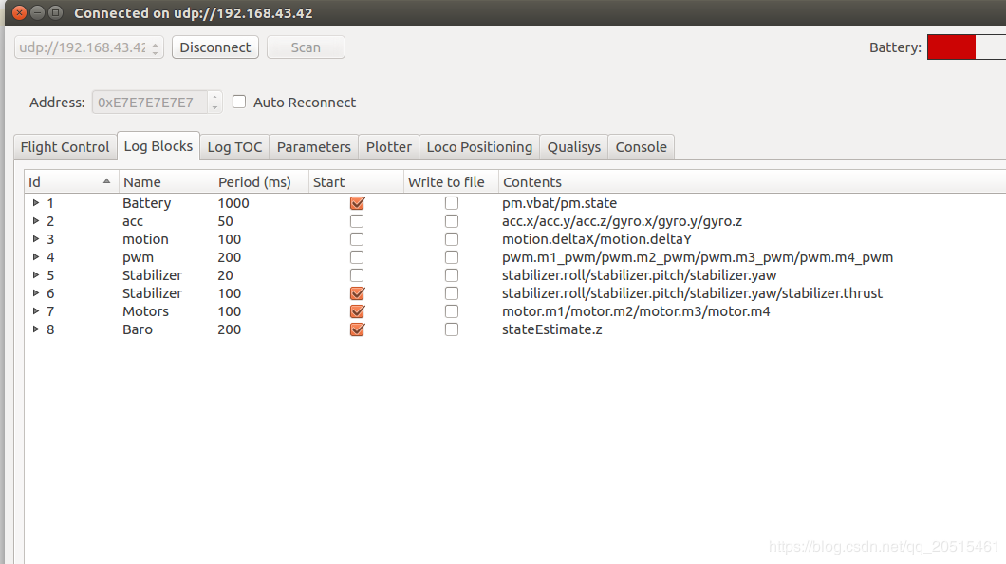
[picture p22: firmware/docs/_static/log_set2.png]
Log Blocks

   
   Log Blocks

Configure real-time waveform drawing at Tab Plotter, to monitor gyro accelerometer data.

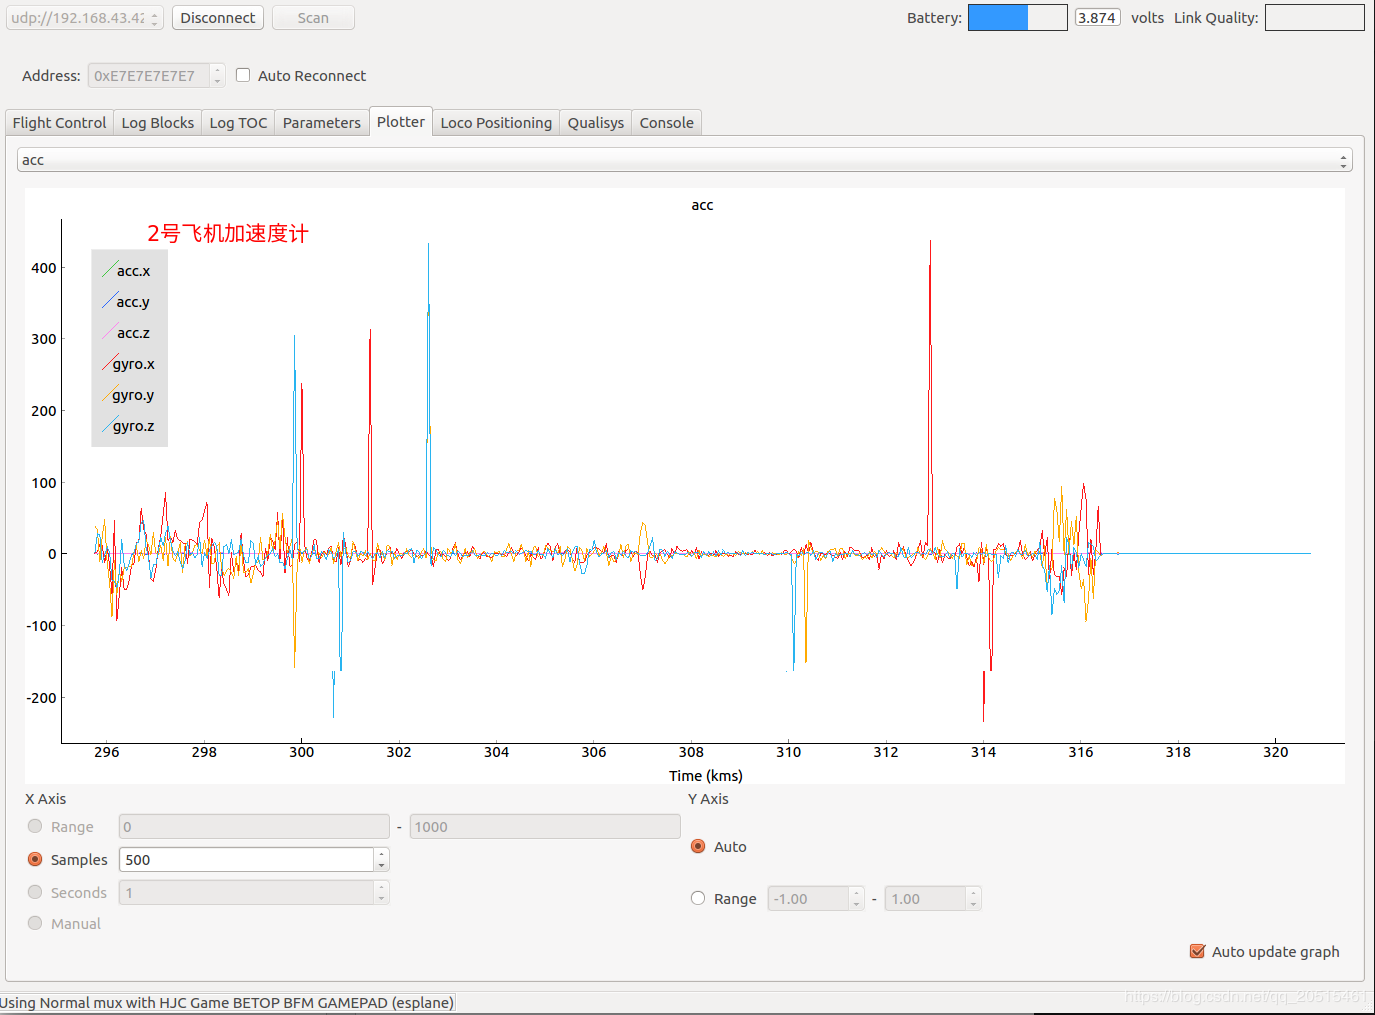
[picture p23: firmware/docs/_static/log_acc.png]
accelerometer logging


   Accelerometer Logging

Propeller Direction
=======================

- Install A and B propellers according to the figure below.
- During the power-on self-test, check if the propellers spin properly.

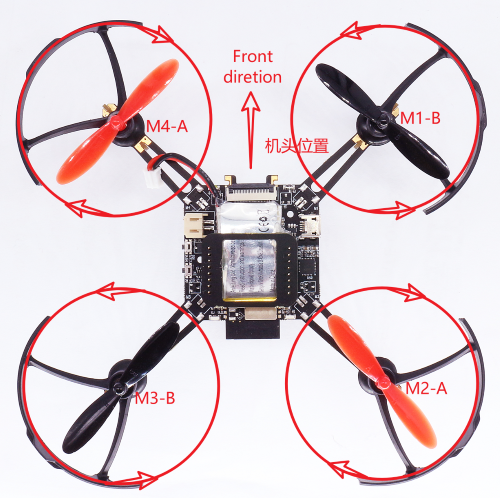
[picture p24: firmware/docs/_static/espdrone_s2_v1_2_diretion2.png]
Propeller check


   Propeller Check

Preflight Check
================

- Place the drone with its head on the front, and its tail (i.e. the antenna part) at the back.
- Place the drone on a level surface and power it up when the drone stays still.
- Check on the cfclient if the drone is placed level.
- After the communication is established, check if the LED at the drone tail blinks GREEN fast.
- Check if the LED on the drone head blinks RED, which indicates battery LOW.
- Slide forward the Trust controller slightly at the left side of your APP (i.e. the commands controlled by your left finger), to check if the drone can respond the command quickly.
- Move your finger at the right command area of the APP (i.e. the commands controlled by your right finger), to check if the direction control works well.
- Go fly and have fun!

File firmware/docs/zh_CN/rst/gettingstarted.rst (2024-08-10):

========
快速入门
========

:link_to_translation:`en:[English]`

项目简介
========

ESP-Drone 是基于乐鑫 ESP32/ESP32-S2/ESP32-S3 开发的小型无人机解决方案，可使用手机 APP 或游戏手柄通过 Wi-Fi
网络进行连接和控制。该方案硬件结构简单，代码架构清晰，支持功能扩展，可用于
STEAM 教育等领域。项目部分代码来自 Crazyflie 开源工程，继承 GPL3.0
开源协议。

ESP-Drone 无人机
   
   ESP-Drone 无人机

主要特性
---------

ESP-Drone 具备以下特性：

-  支持自稳定模式 (Stabilize mode)：自动控制机身水平，保持平稳飞行。
-  支持定高模式 (Height-hold mode)：自动控制油门输出，保持固定高度。
-  支持定点模式 (Position-hold mode)：自动控制机身角度，保持固定空间位置。
-  支持 PC 上位机调试：使用 cfclient 上位机进行静态/动态调试。
-  支持 APP 控制：使用手机 APP 通过 Wi-Fi 轻松控制。
-  支持游戏手柄 (gamepad) 控制：通过 cfclient 使用游戏手柄轻松控制。

主要组件
----------------

ESP-Drone 2.0 使用模块化的设计思路，由主控板和扩展板组成。

-  **主控制板**：搭载 ESP32-S2 模组和支持基础飞行的必要传感器，并提供硬件扩展接口。
-  **扩展板**：搭载扩展传感器，可对接主控制板的硬件扩展接口，支持高级飞行功能。

==== ========================= ========================= ================== ========================== ==============
序号 模块名                    主要元器件                功能               接口                       安装位置
==== ========================= ========================= ================== ========================== ==============
1    主控制板 - **ESP32-S2**   ESP32-S2-WROVER + MPU6050 基础飞行           提供 I2C SPI GPIO 扩展接口
2    扩展板 - **定点模块**     PMW3901 + VL53L1X         室内定点飞行       SPI + I2C                  底部，面向地面
3    扩展板 - **气压定高模块** MS5611 气压               气压定高           I2C 或 MPU6050 从机        顶部或底部
4    扩展板 - **指南针模块**   HMC5883 罗盘              无头模式等高级模式 I2C 或 MPU6050 从机        顶部或底部
==== ========================= ========================= ================== ========================== ==============

详情可查阅：`硬件参考 <./hardware.rst>`__。

ESP-IDF 简介
================

ESP-IDF 是乐鑫为 ESP32/ESP32-S2/ESP32-S3 提供的物联网开发框架。

-  ESP-IDF 包含一系列库及头文件，提供了基于 ESP32/ESP32-S2/ESP32-S3 构建软件项目所需的核心组件。
-  ESP-IDF 还提供了开发和量产过程中最常用的工具及功能，例如：构建、烧录、调试和测量等。

详情可查阅：`ESP-IDF 编程指南 <https://docs.espressif.com/projects/esp-idf/en/release-v4.4/esp32s2/get-started/index.html>`__。

Crazyflie 简介
================

Crazyflie 是来自 Bitcraze 开源工程的四旋翼飞行器，具备以下特性：

-  支持多种传感器组合，可以轻松实现定高模式、定点模式等高级飞行模式。
-  基于 FreeRTOS 编写，将复杂的无人机系统，分解成多个具有不同优先级的软件任务。
-  设计了功能完备的 cfclient 上位机和 CRTP 通信协议，便于实现调试、测量和控制。

crazyflie-overview

   多架无人机同时探索周围环境，灵活避开障碍物，同时避开其它无人机。\ `A
   swarm of drones exploring the environment, avoiding obstacles and
   each other. (Guus Schoonewille, TU
   Delft) <https://img-blog.csdnimg.cn/20191030202634944.jpg?x-oss-process=image/watermark,type_ZmFuZ3poZW5naGVpdGk,shadow_10,text_aHR0cHM6Ly9ibG9nLmNzZG4ubmV0L3FxXzIwNTE1NDYx,size_16,color_FFFFFF,t_70>`__

详情可查阅 `Crazyflie 官网 <https://www.bitcraze.io/>`__。

准备工作
================

硬件组装
----------

请按照下述步骤组装 ESP32-S2-Drone V1.2：

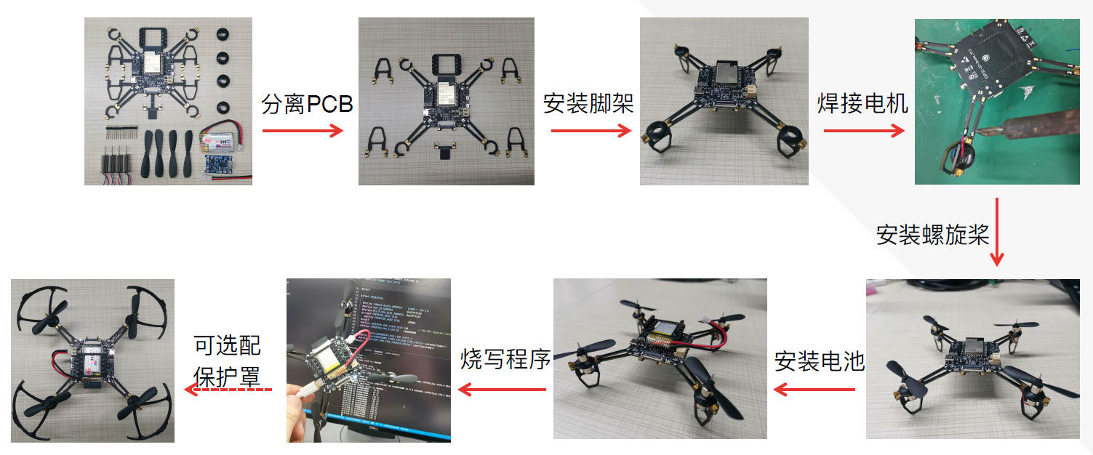
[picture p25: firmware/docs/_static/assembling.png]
ESP32-S2-Drone V1.2 组装流程

   
   ESP32-S2-Drone V1.2 组装流程

硬件介绍和管脚资源分配可查阅：`硬件参考 <./hardware.rst>`__。

安装 ESP-Drone APP
--------------------

ESP-Drone APP 同时支持 Android 系统和 iOS 系统。

**扫描下方二维码，下载 Android APP：**

Android APP 扫码下载

**下载 iOS APP：**

在 App Store 中搜索 ESP-Drone，点击下载并安装。

**iOS APP 源代码**：`ESP-Drone-iOS <https://github.com/EspressifApps/ESP-Drone-iOS>`__

**Android APP 源代码**：`ESP-Drone-Android <https://github.com/EspressifApps/ESP-Drone-Android>`__

安装 cfclient
--------------------

安装 cfclient 为可选步骤，用于实现高级调试，非必须使用。

cfclient 上位机界面

   cfclient 上位机界面

**1. 安装 CRTP 协议支持包**

1.1 下载源代码

.. code:: text

   git clone -b esp-drone  https://github.com/qljz1993/crazyflie-lib-python.git

1.2 进入源码目录，安装依赖

.. code:: text

   pip3 install -r requirements.txt

1.3 安装 CRTP 包

.. code:: text

   pip3 install -e .

**2. 安装 cfclient**

2.1 下载源代码

.. code:: text

   git clone -b esp-drone https://github.com/qljz1993/crazyflie-clients-python.git

2.2 进入源码目录，安装依赖

.. code:: text

   sudo apt-get install python3 python3-pip python3-pyqt5 python3-pyqt5.qtsvg

2.3 安装 cfclient 客户端

.. code:: text

   pip3 install -e .

2.4 启动客户端

.. code:: text

   python3 ./bin/cfclient

**3. 配置遥控器**

游戏手柄配置

   遥控器配置

3.1 配置 4 个控制轴：``Roll 、Pitch、Yaw、Thrust``。

3.2 配置一个按键为 ``Assisted control``，用于飞行模式切换。

手机 APP 使用指南
========================

Wi-Fi 连接
---------------------------
* 手机扫描 Wi-Fi AP。ESP-Drone 设备用作 AP，其 SSID 及密码如下：

::

   SSID：ESP-DRONE_XXXX（XXXX 根据 MAC 设置）PASSWORD：12345678

* 点击该 AP，手机与 ESP-Drone 设备建立 Wi-Fi 连接。

个性化设置
-----------

在该步骤中，您可以按照具体的应用场景进行个性化配置，或使用默认配置。

::

   ```
   默认配置：

   Flight control settings 
       1. Mode: Mode2
       2. Deadzone: 0.2
       3. Roll trim: 0.0
       4. Pitch trim: 0.0
       5. Advanced flight control : true
       6. Advanced flight control preferences 
           1. max roll/pitch angle: 15
           2. max yaw angle: 90
           3. max thrust: 90
           4. min thrust: 25
           5. X-Mode: true
   Controller settings 
       1. use full travel for thrust: false
       2. virtual joystick size: 100
   App settings
       1. Screen rotation lock: true
       2. full screen mode:true
       3. show console: true   
   ```

控制飞行
--------

-  打开 APP，点击 `Connect` 按钮，连接小飞机。连接成功，小飞机绿灯闪烁。
-  轻推油门，小飞机起飞。
-  在 APP 上滑动，控制小飞机方向。

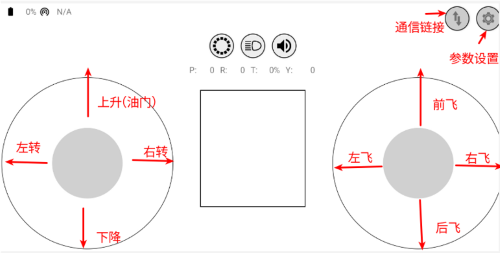
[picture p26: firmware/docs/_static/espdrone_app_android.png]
Android APP 用户界面


   Android APP 用户界面

PC cfclient 使用指南
========================

cfclient 是 ``Crazeflie`` 源工程的上位机，完全实现了 ``CRTP``
协议中定义的功能，可以加快飞机的调试过程。ESP-Drone
项目对该上位机进行裁剪和调整，满足功能设计需求。

cfclient 架构

   cfclient 架构

cfclient 控制台界面

   cfclient 控制台界面

项目中有很多相关的文件，例如配置文件和缓存文件，其中 JSON
文件用来存储配置信息。关于配置信息中内容的解读，可参考：`User
Configuration
File <https://www.bitcraze.io/documentation/repository/crazyflie-clients-python/master/development/dev_info_client/>`__。

飞行设置
----------

基本飞行设置 (Basic Flight Control)
~~~~~~~~~~~~~~~~~~~~~~~~~~~~~~~~~~~~~

1. 飞行模式 (Flight mode)：基本模式和高级模式

   -  基本模式 (Normal mode)：初学者使用。
   -  高级模式 (Advanced mode)：设置解锁最大角度，设置最大油门。

2. 自动模式 (Assisted mode)

   -  定海拔模式 (Altitude-hold mode)：保持飞行海拔，需要气压计支持。
   -  定点模式 (Position-hold mode)：保持当前位置，需要光流和 TOF 支持。
   -  定高模式 (Height-hold mode)：保持相对高度，触发时保持高于地面 40
      cm，需要 TOF 支持。
   -  悬停模式 (Hover mode)：触发时保持高于地面 40
      cm，并悬停在起飞点，需要光流和 TOF 支持。

3. 角度修正 (Trim)

   -  翻滚角修正 (Roll Trim)：用于弥补传感器水平安装误差。
   -  俯仰角修正 (Pitch Trim)：用于弥补传感器水平安装误差。

注意，在自动模式下，油门摇杆变为高度控制摇杆。

高级飞行设置 (Advanced Flight Control)
~~~~~~~~~~~~~~~~~~~~~~~~~~~~~~~~~~~~~~

1. 最大倾角 (Max angle)：设置最大允许的俯仰和翻滚角度：roll/pitch。
2. 最大自旋速度 (Max yaw rate)：设置允许的偏航速度：yaw。
3. 最大油门 (Max thrust)：设置最大油门。
4. 最小油门 (Min thrust)：设置最小油门。
5. 压摆极限 (Slew limit)：防止油门骤降，油门低于该值时，下降速度将被限定。
6. 压摆率 (Slew rate)：油门到压摆极限之后的最大下降率。

遥控器设置 (Configure Input Device)
~~~~~~~~~~~~~~~~~~~~~~~~~~~~~~~~~~~~~~

按照提示绑定遥控器摇杆与各个控制通道：

cfclient 控制器配置

飞行数据 (Flight Data)
~~~~~~~~~~~~~~~~~~~~~~~~~~

驾驶仪可以看到当前飞机姿态，右下方显示对应的详细数据。

1. 目标角度 (Target)
2. 测量角度 (Actual)
3. 当前油门值 (Thrust)
4. 电机实际输出 (M1/M2/M3/M4)

在线参数修改
--------------------

**在线调整 PID 参数**

PID 参数调整
   
   cfclient PID 参数调整

**注意事项**

1. 修改的参数实时生效，避免了频繁烧录固件。
2. 可在代码中通过宏定义，配置哪些参数可被上位机实时修改。
3. 注意，参数在线修改仅用于调试，掉电不保存。

飞行数据监控
--------------------

**配置要监控的参数**

PID 参数调整

   监控参数配置

PID 参数调整

   参数配置区

**实时波形绘制**

陀螺仪加速度计实时数据监测：

PID 参数调整

   陀螺仪加速度计数据监测

螺旋桨方向
================

-  按照下图所示位置，安装 A、B 螺旋桨。
-  飞行器上电自检时，检查螺旋桨转向是否正确。

螺旋桨方向示图

   螺旋桨方向示图

起飞前检查
================

-  将小飞机头部朝前放置，尾部天线朝向自己；
-  将小飞机置于水平面上，待机身稳定时上电；
-  观察上位机水平面是否置平；
-  观察通信建立以后，小飞机尾部绿灯是否快速闪烁；
-  观察小飞机头部红灯是否熄灭，亮起代表电量不足；
-  轻推左手小油门，检查飞机是否能快速响应；
-  轻推右手方向，检查方向控制是否正确；
-  起飞吧！

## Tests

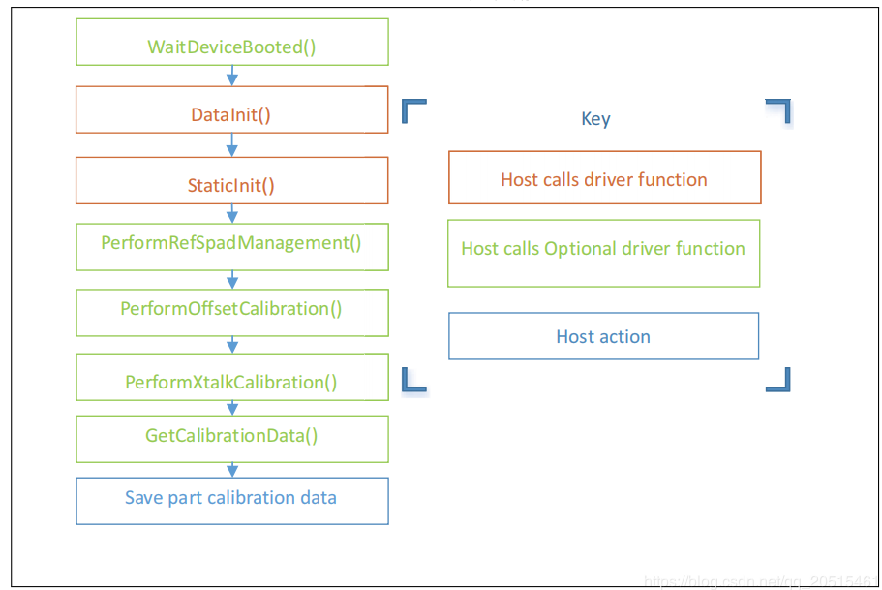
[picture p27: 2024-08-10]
firmware/docs/_static/vl53lxx_calibration_sequence.png

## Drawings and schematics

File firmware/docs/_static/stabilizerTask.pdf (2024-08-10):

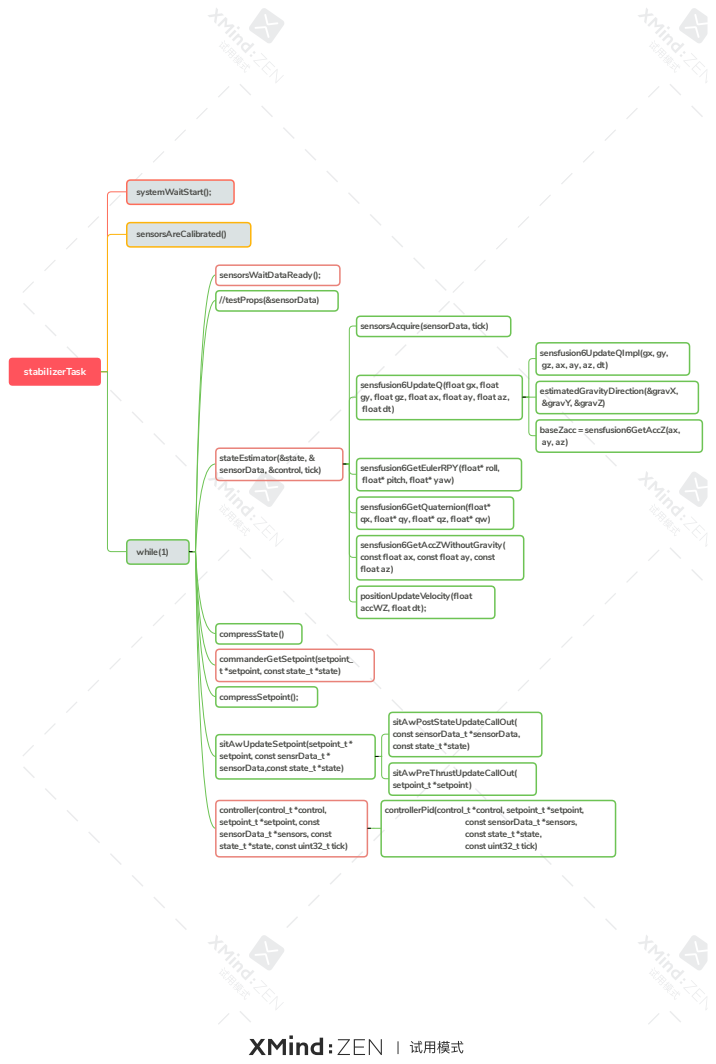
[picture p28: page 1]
stabilizerTask; systemWaitStart();; sensorsAreCalibrated(); while(1); sensorsWaitDataReady();; //testProps(&sensorData); estimatedGravityDirection(&gravX, &gravY, &gravZ); baseZacc = sensfusion6GetAccZ(ax, ay, az); compressState(); compressSetpoint();; sitAwPostStateUpdateCallOut( const sensorData_t *sensorData, const state_t *state); sitAwPreThrustUpdateCallOut( setpoint_t *setpoint)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

sensorsAcquire(sensorData, tick)

sensfusion6UpdateQImpl(gx, gy,

sensfusion6UpdateQ(float gx, float
gy, float gz, float ax, float ay, float az,
float dt)

stateEstimator(&state, &
sensorData, &control, tick)

sensfusion6GetEulerRPY(float* roll,
float* pitch, float* yaw)

sensfusion6GetQuaternion(float*
qx, float* qy, float* qz, float* qw)

sensfusion6GetAccZWithoutGravity(
const float ax, const float ay, const
float az)

positionUpdateVelocity(float
accWZ, float dt);

commanderGetSetpoint(setpoint_
t *setpoint, const state_t *state)

sitAwUpdateSetpoint(setpoint_t *
setpoint, const sensrData_t *
sensorData,const state_t *state)

controllerPid(control_t *control, setpoint_t *setpoint,

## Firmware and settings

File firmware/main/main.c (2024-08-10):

/*
 * ESP-Drone Firmware
 * 
 * Copyright 2019-2020  Espressif Systems (Shanghai) 
 * Copyright (C) 2011-2012 Bitcraze AB
 *
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
 */

#include <stdint.h>
#include <stdio.h>
#include <stdlib.h>

#include "freertos/FreeRTOS.h"
#include "freertos/task.h"
#include "freertos/portmacro.h"
#include "nvs_flash.h"

#include "stm32_legacy.h"
#include "platform.h"
#include "system.h"
#define DEBUG_MODULE "APP_MAIN"
#include "debug_cf.h"

void app_main()
{
    /*
    * Initialize the platform and Launch the system task
    * app_main will initialize and start everything
    */

    /* initialize nvs flash prepare for Wi-Fi */
    esp_err_t ret = nvs_flash_init();

    if (ret == ESP_ERR_NVS_NO_FREE_PAGES || ret == ESP_ERR_NVS_NEW_VERSION_FOUND) {
        ESP_ERROR_CHECK(nvs_flash_erase());
        ret = nvs_flash_init();
    }

    ESP_ERROR_CHECK(ret);

    /*Initialize the platform.*/
    if (platformInit() == false) {
        while (1);//if  firmware is running on the wrong hardware, Halt
    }

    /*launch the system task */
    systemLaunch();

}

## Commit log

2024-08-10 Create 3D frame
2024-08-10 uploaded drone frame
    [FE2G7MWIGL8J36N.stl]
2024-09-02 Update sensors_mpu6050_hm5883L_ms5611.c
    Disabled Barometer by default
2024-09-25 Update sensors_mpu6050_hm5883L_ms5611.c
    changed gyro direction
2024-09-30 Update sensors_mpu6050_hm5883L_ms5611.c
    changed gyro orientation
2024-10-13 Update sensors_mpu6050_hm5883L_ms5611.c
    FIXED MS5611 not giving pressure updates after initialisation. (Took 2 freaking weeks)

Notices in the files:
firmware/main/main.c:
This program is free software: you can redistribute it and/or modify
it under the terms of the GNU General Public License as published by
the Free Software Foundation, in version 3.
